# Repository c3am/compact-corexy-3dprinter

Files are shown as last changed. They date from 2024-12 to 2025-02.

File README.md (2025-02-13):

# compact corexy 3d-printer

the printer

The [corexy motion system](https://corexy.com/) is not only useful because of its small
moving mass, but also because of the compact and easily enclosable form factor,
but all the popular diy printers that use it are kind of expensive.
So I designed a corexy 3d printer that has most of the common features of a modern enclosed
machine while trying to keep it affordable.

Caution! This printer is still in active development and not yet thoroughly tested.

## general goals:
- good print quality at 20mm^3/s 0.5mm width 0.25mm height
- able to print PLA, PETG and ABS reliably
- (180mm)^3 build volume
- easy to build and maintain
- as affordable as possible
- as compact as possible
- have an exaust/filter system
- be as quiet as possible

## specs:
- frame
    - size: 356mm * 356mm * 456mm outer dimensions
    - made out of 2020 v-slot aluminium extrusions
    - panels can be lasercut out of 3mm MDF and/or acrylic
    - easy to assemble 3d printed frame corners
    - z-motion system integrated in bottom corners and skirts

- motion system
    - xy-motors at the front move for belt tesnioning
    - 3-point belt driven z-axis, only 1 stepper
    - 250mm * 8mm linear rods for y- and z-axis
    - 250mm mgn9h for x-axis
    - (180mm)^3 build volume

- toolhead
    - bondtech extruder gears, 36mm stepper
    - tz 2.0 bambulab clone hotend
    - inductive bed probe                                   (in development)
    - ebb36 toolhead board                                  (in development)

- air management
    - 80mm air exhaust port (possible to attatch filter)
    - 12032 radial fan 22mm cpap part cooling               (in development)
    - active 65W heater                                     (in development)

- electronics
    - Klipper running on rpi zero 2 W
    - mainboard: skr mini e3 v2.0
    - cheap 24V 10A PSU
    - custom CAN BUS board for active heater                (in development)

## BOM
The BOM is a libreoffice spreadsheet document called BOM.ods.
I have included links to where i buy the parts. Depending on where you live you might
need to find another supplier though. The material costs are at roughly 320 Eur and can vary
depending on whether you buy in bulk or just for one printer.

## CAD software

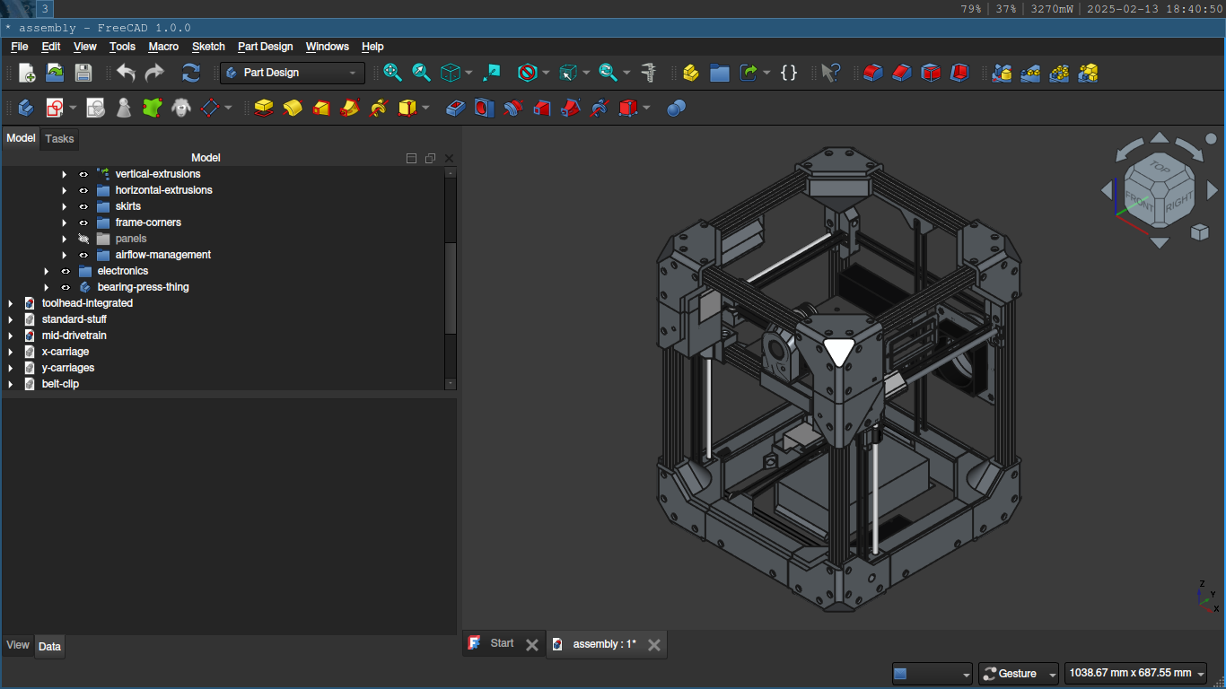
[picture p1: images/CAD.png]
a cad view of the printer


This project uses FreeCAD. All the CAD files are in the CAD folder.
Currently there are no plugins you need to install to open any of the CAD files.
There is one main assembly file where all the parts of the printer are integrated.
You can't just download the assembly.FCStd file because it uses links to integrate all the other
sub-assemblies or parts from the other files. You have to download the whole repository (or the CAD folder)
in order to open the main assembly file.

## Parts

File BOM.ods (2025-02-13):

Name | Einzelpreis | Anzahl | Gesamtpreis |  | not necessary for minimal setup
toolhead |  |  | 46.87 €
Tz 2.0 hotend kit | 10.00 € | 1 | 10.00 € | https://de.aliexpress.com/item/1005007319888761.html |  | 0
bowden tube (1m) | 2.00 € | 0.5 | 1.00 € | https://de.aliexpress.com/item/32948527208.html |  | 0
bondtech clone extruder gears | 5.00 € | 1 | 5.00 € | https://de.aliexpress.com/item/1005005629301296.html |  | 0
36mm round stepper motor | 8.19 € | 1 | 8.19 € | https://de.aliexpress.com/item/1005007413260278.html |  | 0
ebb36 toolhead board | 15.79 € | 1 | 15.79 € | https://de.aliexpress.com/item/1005004242943483.html | x | 15.79 €
inductive probe | 4.19 € | 1 | 4.19 € | https://de.aliexpress.com/item/1005001999669147.html | x | 4.19 €
20mm cpap tube 1.8m | 5.39 € | 0.5 | 2.70 € | https://de.aliexpress.com/item/1005006807889428.html | x | 2.70 €
 |  |  |  |  |  | 0
bed |  |  | 20.00 € |  |  | 0
180mm heated bed | 10.00 € | 1 | 10.00 € | https://de.aliexpress.com/item/1005007288279620.html |  | 0
PEI sheet | 10.00 € | 1 | 10.00 € | https://de.aliexpress.com/item/1005006524934536.html |  | 0.00 €
 |  |  |  |  |  | 0
motion system |  |  | 88.33 € |  |  | 0
Nema 17 stepper motor | 7.50 € | 3 | 22.50 € | https://www.ebay.de/itm/204393931481 |  | 0
gt2 belt 5m | 4.00 € | 1 | 4.00 € | https://de.aliexpress.com/item/32913580172.html |  | 0
pulley gt2 16t 5mm | 1.00 € | 1 | 1.00 € | https://de.aliexpress.com/item/1005001933418605.html |  | 0
pulley gt2 20t 5mm | 1.00 € | 2 | 2.00 € |  |  | 0
pulley gt2 20t 8mm | 1.00 € | 4 | 4.00 € |  |  | 0
pulley gt2 32t 8mm | 2.00 € | 2 | 4.00 € | https://de.aliexpress.com/item/1005006631599374.html |  | 0
idler kit gt2 20t 5mm id 15mm od | 7.19 € | 1 | 7.19 € | https://de.aliexpress.com/item/1005005767406346.html |  | 0
idler gt2 20t toothed | 1.00 € | 4 | 4.00 € | https://de.aliexpress.com/item/1005002630474461.html |  | 0
idler gt2 20t smooth | 1.00 € | 2 | 2.00 € |  |  | 0
stainless steel rod 8mm 1m | 3.26 € | 1 | 3.26 € | https://www.ebay.de/itm/283092189576 |  | 0.00 €
608 bearing | 0.50 € | 7 | 3.50 € | https://www.ebay.de/itm/316177978508 |  | 0.00 €
smooth rod 8mm 250mm | 3.47 € | 4 | 13.88 € | https://de.aliexpress.com/item/1005005720978294.html |  | 0.00 €
lm8uu bearing | 1.00 € | 2 | 2.00 € | https://robotdigg.com/product/872/Quality-LM8UU-or-LME8UU-Linear-Bearing |  | 0.00 €
lm8luu bearing | 2.00 € | 2 | 4.00 € | https://robotdigg.com/product/873/Quality-LM8LUU-Linear-Bearing |  | 0.00 €
mgn9 rail 250mm + mgn9h carriage | 11.00 € | 1 | 11.00 € | https://robotdigg.com/product/631/GCr15-MGN9-L200,-L250,-L300-linear-rail-n-carriage |  | 0.00 €
 |  |  |  |  |  | 0
frame |  |  | 37.64 € |  |  | 0
2020 * 300mm aluminium extrusion | 1.45 € | 8 | 11.60 € | https://www.aluxprofile.com/aluminium-slot-profile-2020-v-slot/a3663 |  | 0
2020 * 400mm aluminium extrusion | 1.93 € | 4 | 7.72 € |  |  | 0
2020 * 280mm aluminium extrusion | 1.35 € | 1 | 1.35 € |  |  | 0
2020 * 200mm alumium extrusion | 0.97 € | 1 | 0.97 € |  |  | 0
3mm MDF panel 400mm * 500mm | 1.00 € | 6 | 6.00 € | locally sourced | x | 6.00 €
3mm plexiglas door panels | 10.00 € | 1 | 10.00 € | locally sourced | x | 10.00 €
 |  |  |  |  |  | 0
electronics |  |  | 96.63 € |  |  | 0
bigtreetech skr mini e3 v2.0 | 25.00 € | 1 | 25.00 € | https://de.aliexpress.com/item/1005006394605188.html |  | 0
raspberry pi zero 2 w + usb otg cable | 20.70 € | 1 | 20.70 € | https://www.berrybase.de/raspberry-pi-zero-2-w |  | 0.00 €
24V 10A PSU | 15.99 € | 1 | 15.99 € | https://www.ebay.de/itm/266206392908 |  | 0
C13 port with fuse and switch | 4.80 € | 1 | 4.80 € | https://www.ebay.de/itm/116128616501 |  | 0
12032 24V radial part cooling fan | 15.79 € | 1 | 15.79 € | https://de.aliexpress.com/item/1005003168863416.html or https://www.ebay.de/itm/305590042695 | x | 15.79 €
8025 24V exhaust fan | 4.16 € | 1 | 4.16 € | https://www.ebay.de/itm/176149077551 | x | 4.16 €
5020 24V heater fan | 2.00 € | 1 | 2.00 € | https://de.aliexpress.com/item/1902954753.html | x | 2.00 €
PTC heater 24V 65W | 5.19 € | 1 | 5.19 € | https://de.aliexpress.com/item/1005001849494940.html | x | 5.19 €
heater control board | 3.00 € | 1 | 3.00 € | To be developed | x | 3.00 €
 |  |  |  |  |  | 0.00 €
fasteners |  |  | 27.00 € |  |  | 0.00 €
bhcs m5 * 8mm | 0.10 € | 96 | 9.60 € | locally sourced |  | 0.00 €
bhcs m5 * 20mm | 0.15 € | 16 | 2.40 € |  |  | 0.00 €
2020 m5 t-nut | 0.05 € | 100 | 5.00 € |  |  | 0.00 €
2020 m5 twisting t-nut | 0.05 € | 100 | 5.00 € |  |  | 0.00 €
shcs m3 * 10mm | 0.05 € | 40 | 2.00 € |  |  | 0.00 €
shcs m3 * 30mm | 0.10 € | 20 | 2.00 € |  |  | 0.00 €
m3 nut | 0.01 € | 100 | 1.00 € |  |  | 0.00 €
TOTAL: |  |  | 316.47 € |  |  | 68.815
 |  |  |  |  |  | 247.65 €

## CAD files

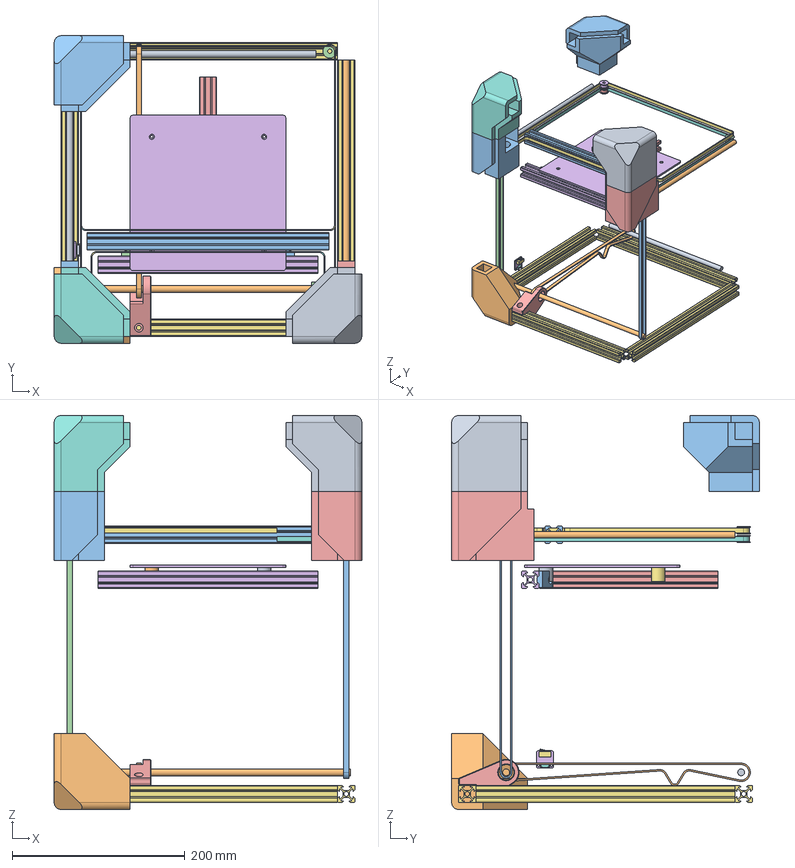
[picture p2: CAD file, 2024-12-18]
CAD/assembly.FCStd
356.0 x 356.0 x 456.0 mm
z-motion-back-rod
z-motion-front-rod
z-motion-front-belt-right
z-motion-front-belt-left
z-motion-bearing-block-mid
endstop-pcb002
endstop-switch-body002
endstop-connector002
switch-arm002
z-motion-mid-belt
x-extrusion
idler-back-right-top (Mirror #9) x 2
idler-back-right-top (Mirror #10) x 2
idler-back-right-top (Mirror #11) x 2
xy-belt-1
xy-belt-2
y-rod-left
y-rod-right
xy-motor-mount-left
xy-motor-right x 2
xy-motor-mount-right
heated-bed
bed-standoff-1 x 2
bed-standoff-2 x 2
bed-standoff-3 x 2
bed-standoff-4 x 2
bed-mount-1
bed-mount-2 x 2
extrusion-mid
extrusion-back
horizontal-extrusions-top x 2
frame-corner-top-front-left x 2
frame-corner-top-front-right x 2
frame-corner-bottom-front-left x 2
frame-corner-top-back-left x 2

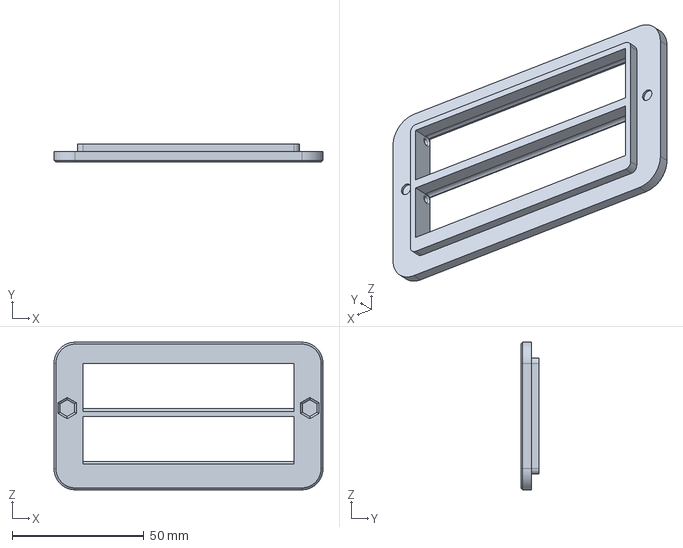
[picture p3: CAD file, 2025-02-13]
CAD/air-management/intake-vents.FCStd
102.0 x 7.00 x 56.0 mm

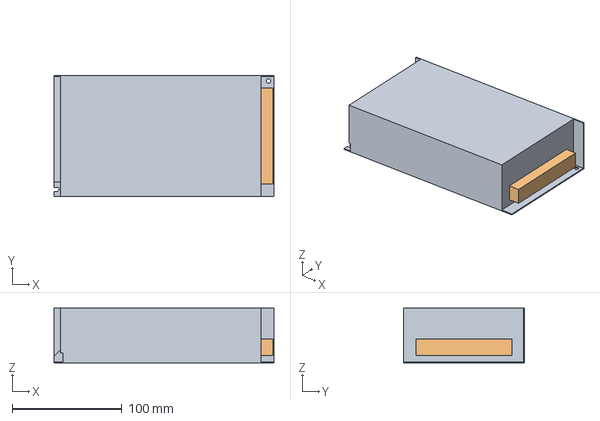
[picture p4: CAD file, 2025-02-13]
CAD/electronics/PSU-12V-10A.FCStd
200.0 x 110.0 x 50.0 mm
terminal-block

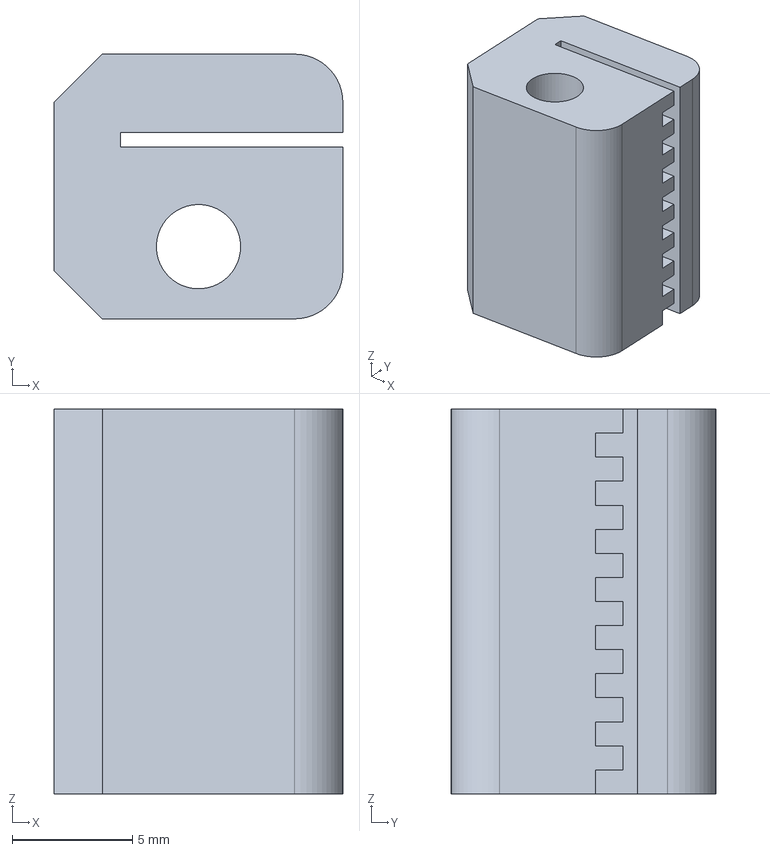
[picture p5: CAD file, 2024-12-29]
CAD/general/belt-clip.FCStd
12.0 x 11.0 x 16.0 mm

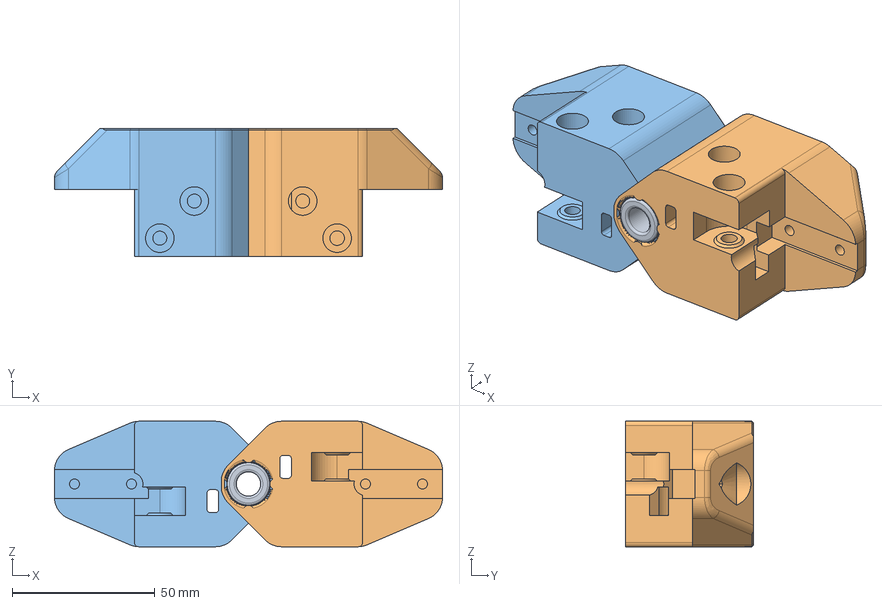
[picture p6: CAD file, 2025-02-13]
CAD/xy-gantry/y-carriages.FCStd
136.0 x 45.0 x 44.0 mm
lm8luu-bearing-drv
y-carriage-left
y-carriage-right

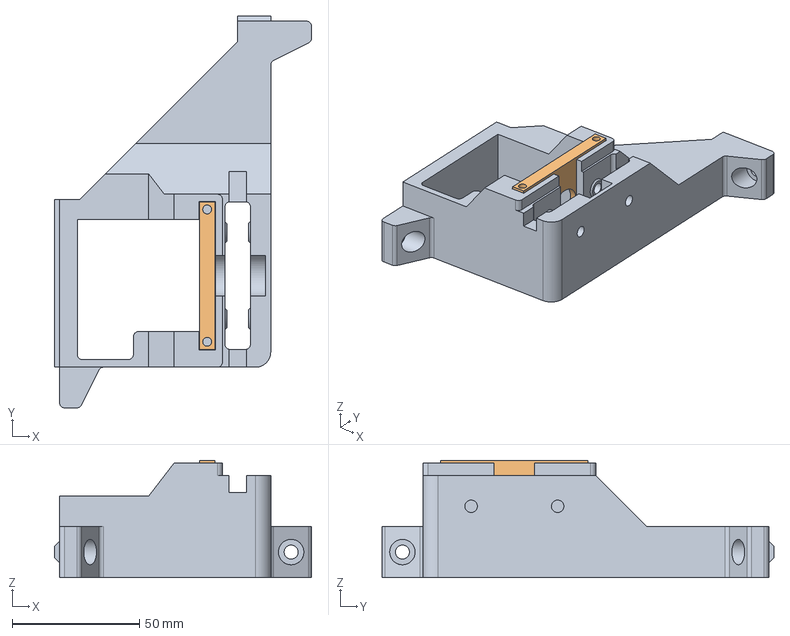
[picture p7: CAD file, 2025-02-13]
CAD/z-motion/mid-drivetrain.FCStd
101.0 x 154.0 x 46.0 mm
z-motion-mid-drivetrain
z-motion-mid-motor-mount

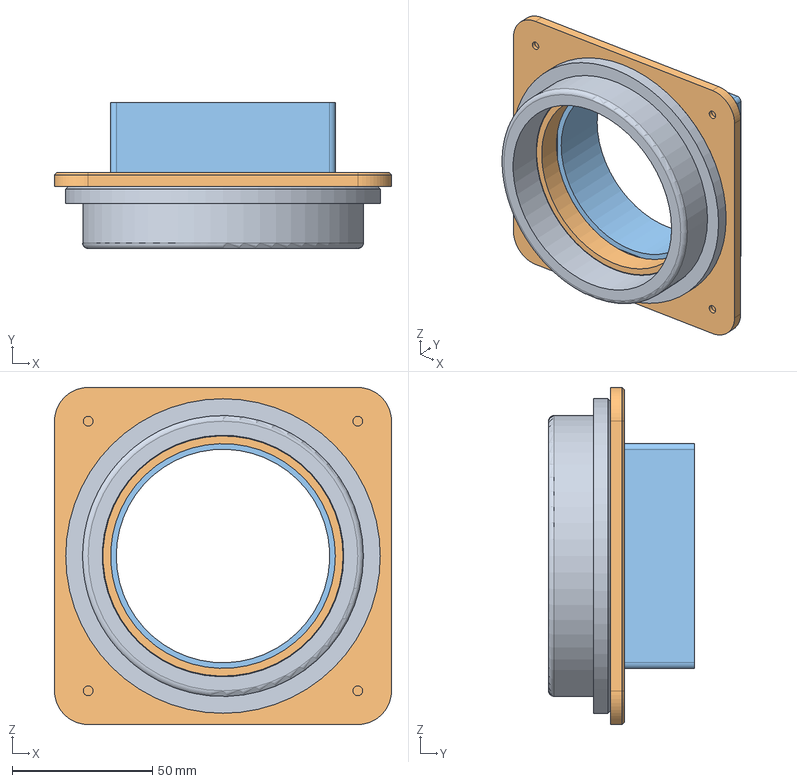
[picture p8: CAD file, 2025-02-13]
CAD/air-management/air-exhaust.FCStd
120.0 x 52.0 x 120.0 mm
air-connector-hose
air-connector-chamber
exhaust-fan

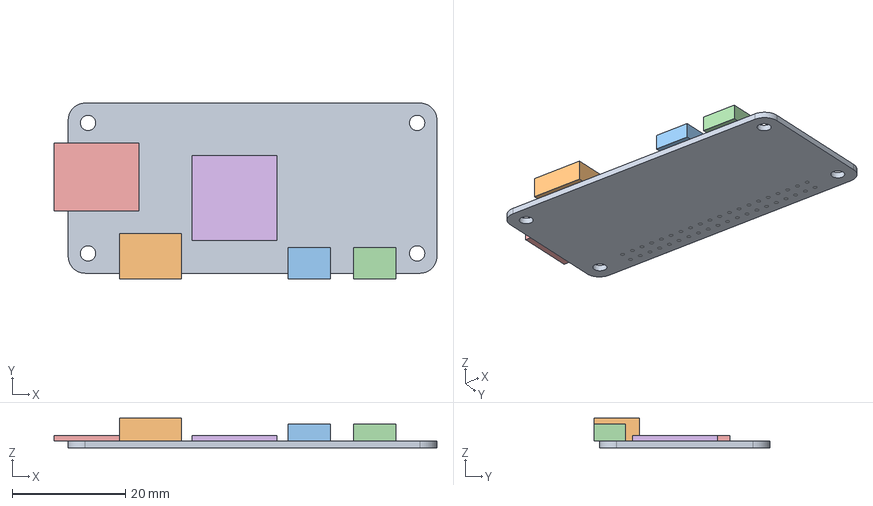
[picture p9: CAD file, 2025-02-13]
CAD/electronics/pi-zero-2-w.FCStd
67.5 x 31.0 x 5.20 mm
PCB
mini-hdmi
usb-power
usb-data
sd-card-slot
cpu

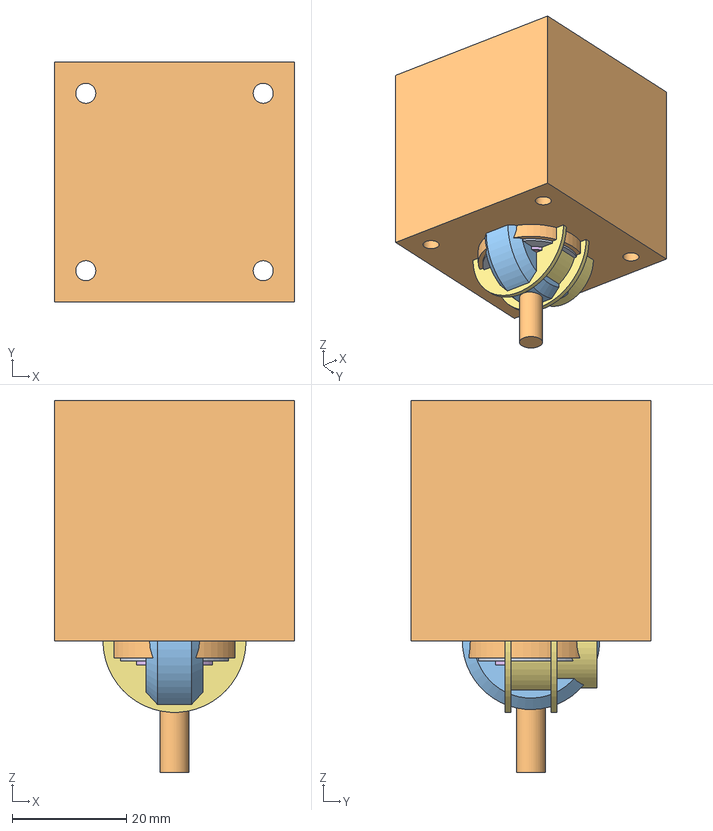
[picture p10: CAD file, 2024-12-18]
CAD/general/standard-stuff.FCStd
42.0 x 42.0 x 65.0 mm
bearing-608
nema-17
v-wheel
pulley-16t-5mm
pulley-20t-8mm
idler-20t
pulley-32t-8mm
pulley-20t-5mm

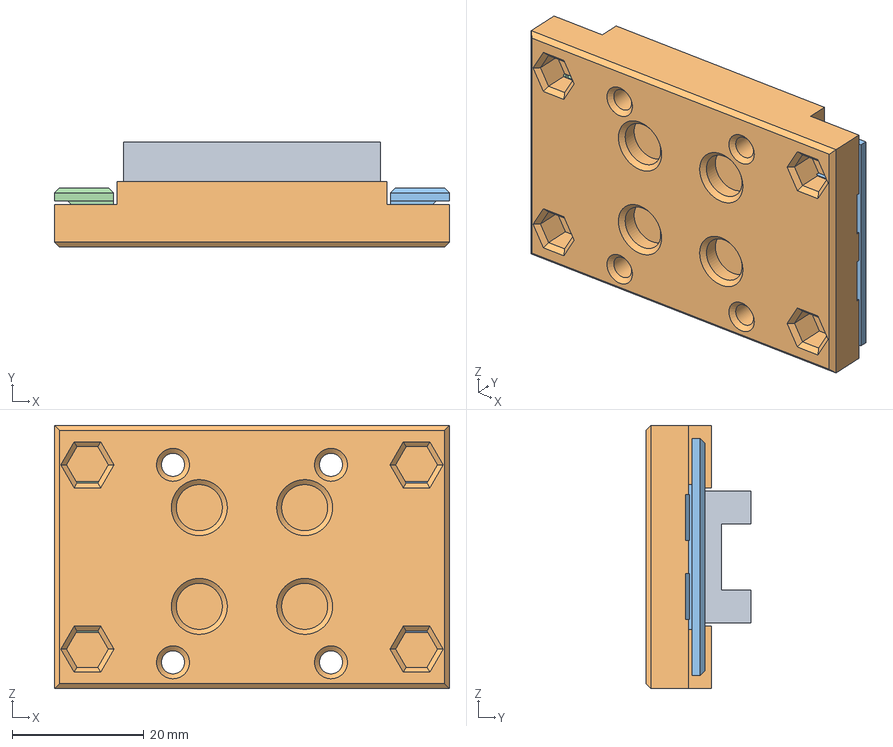
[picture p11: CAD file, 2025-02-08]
CAD/xy-gantry/x-carriage.FCStd
60.0 x 16.0 x 40.0 mm
mgn9h-carriage-x
x-carriage
belt-clamp-right
belt-clamp-left

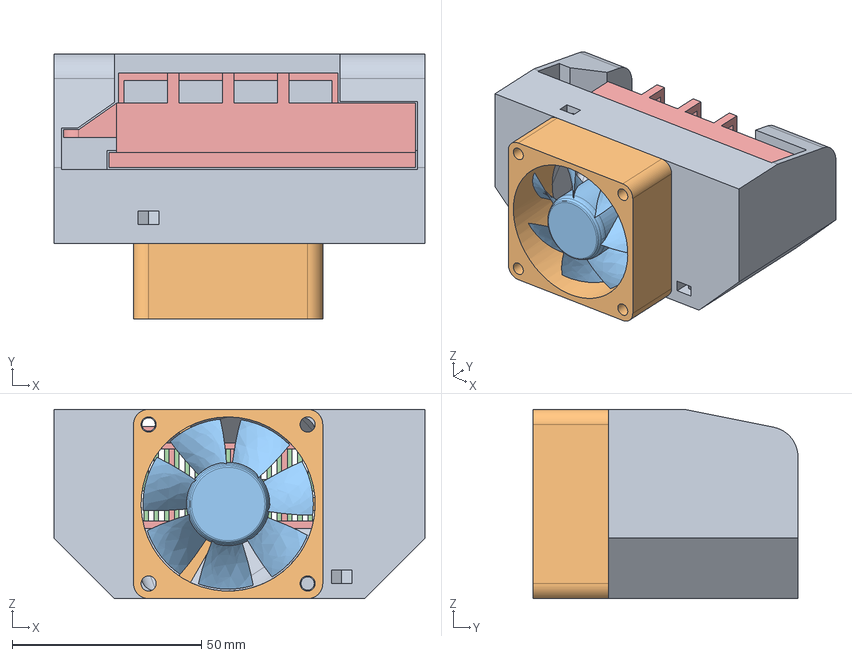
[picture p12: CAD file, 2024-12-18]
CAD/air-management/chamber-heater.FCStd
98.0 x 70.0 x 50.0 mm
housing
5020-fan-base-drv
5020-fan-rotor-drv
heater-core-drv
heater-case-drv

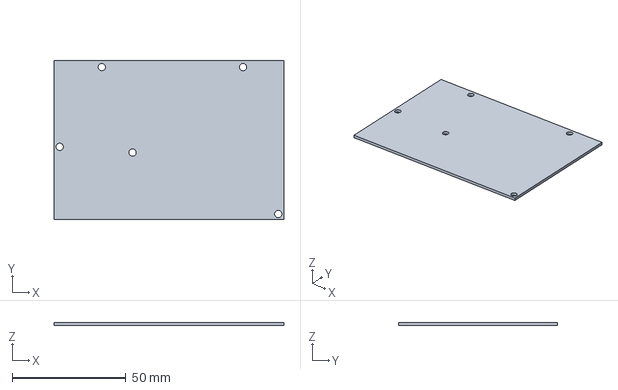
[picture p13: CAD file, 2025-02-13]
CAD/electronics/bigtreetech-mini-e3-v2.0.FCStd
101.0 x 70.0 x 1.40 mm

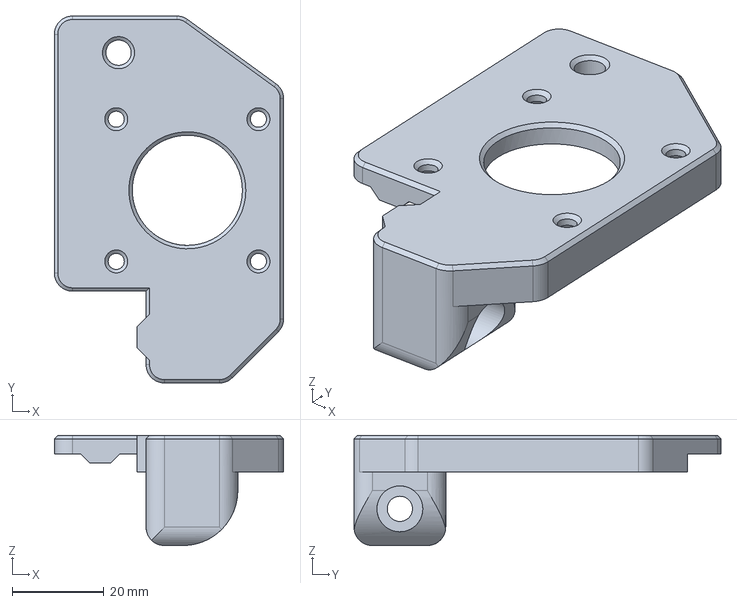
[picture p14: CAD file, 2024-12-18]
CAD/xy-gantry/motor-mounts.FCStd
50.0 x 80.0 x 24.0 mm

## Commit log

2024-12-18 made up a cool structure
    [PSU-12V-10A.FCStd, air-hose-connector.FCStd, assembly-electronics-mounting-plate.stl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]
2024-12-29 base version of the printer without panels or exhaust stuff or chamber heater
    [PSU-12V-10A.FCStd, air-hose-connector.FCStd, assembly-electronics-mounting-plate.stl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]
2025-02-05 added a lot of stuff including motor mount tensioning
    [PSU-12V-10A.FCStd, assembly-frameframe-corner-top-front-left.stl, assembly-mainboard-mount.stl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]
2025-02-08 added clearance for x-carriage belt mounting
    [PSU-12V-10A.FCStd, air-hose-connector.FCStd, assembly-mainboard-mount.stl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]
2025-02-13 re-did the readme, added air exhaust
    [BOM.ods, PSU-12V-10A.FCStd, air-exhaust.FCStd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]
2025-02-13 removed outdated printed-parts file, removed stl files
    [assembly-mainboard-mount.stl, assembly-xy-gantryz-rod-clamp-left.stl, assembly-xy-gantryz-rod-clamp-right.stl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]
2025-02-13 removed unnecessary cad files, restructured cad files
    [air-exhaust.FCStd, belt-clip.FCStd, chamber-heater.FCStd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]
2025-02-13 restored broken freecad links
    [mid-drivetrain.FCStd, y-carriages.FCStd]
